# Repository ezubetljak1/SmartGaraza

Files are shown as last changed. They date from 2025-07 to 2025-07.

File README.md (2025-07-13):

# IoT Pametni Garažni Sistem

U današnje doba Interneta Stvari, svakodnevni uređaji postaju pametniji i povezaniji. Ovaj projekt pretvara običnu garažu u siguran i jednostavan sistem za pristup integracijom:

- **Višefaktorski pristup**: RFID čip, PIN kod ili mobilna aplikacija  
- **Evidencija pristupa**: Svaki ulaz/izlaz bilježi se sa vremenom pristupa i ID‑om korisnika  
- **Zaštita od neovlaštenih upada**: Automatsko zaključavanje i obavijest vlasniku o pokušaju pristupa  
- **Daljinsko upravljanje**: Otvarajte ili nadgledajte garažu putem aplikacije, odakle god želite

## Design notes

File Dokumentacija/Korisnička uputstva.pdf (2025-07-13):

Univerzitet u Sarajevu
Elektrotehnički fakultet

Ugradbeni sistemi (RI/TK) 2024/25

# Sistem za upravljanje pristupom garaži pomoću IoT tehnologija

## Korisnička uputstva

Članovi tima:

Dalila Tanković | 19665
Emina Hadžić | 19798
Emina Zubetljak | 19676
30. 6. 2025. god.

## Sadržaj

## 1 O proizvodu

Ovim putem Vam se zahvaljujemo što ste se odlučili za korištenje našeg pametnog sistema za kontrolu garažnih vrata. Naš cilj je da uživate u svim pogodnostima koje Vam on donosi, najprije u sigurnosti, pouzdanosti, te jednostavnosti korištenja.

Ovaj sistem koristi najnovije tehnologije iz oblasti ugradbenih mikrokontrolera i Interneta Stvari, kako bi Vam omogućio:

- jednostavno i brzo otvaranje garažnih vrata,
- sigurnu kontrolu pristupa za članove domaćinstva,
- daljinsko upravljanje putem mobilne aplikacije,
- zaštitu od neovlaštenog ulaska zahvaljujući ugrađenom alarmnom sistemu.

Uputstva koja slijede Vam služe za pravilno korištenje i održavanje uređaja.

## 2 Sastav sistema

Sistem se sastoji od više komponenti. Detaljnije možete pročitati u idućoj tabeli.

Tabela 1: Komponente i namjene u sistemu garaže

Komponenta | Namjena
picoETF kontroler | Vanjska jedinica – kontrola pristupa
Ultrazvučni senzor | Detekcija vozila ispred garaže
RFID čitač | Očitavanje beskontaktnih kartica
Tastatura | Unos sigurnosnog PIN koda
Piezo zvučnik | Alarmni sistem
LED dioda | Vizuelni indikator statusa alarma
Servo motor | Otvaranje i zatvaranje vrata
Touch senzor | Lokalno otvaranje/zatvaranje vrata
picoETF kontroler | Unutrašnja jedinica garaže

## 3 Sigurnosna upozorenja

Upozorenje! Nikada nemojte gurati ili silom pomjerati vrata dok ih upravlja motor.

Napomena! Samo osobe sa validnom karticom ili PIN kodom mogu otvoriti vrata.

Preporuka! Koristite mobilnu aplikaciju za nadzor i u hitnim slučajevima.

## 4 Osnovne upute

### 4.1 Dolazak vozila

Kada automobil priđe garaži, ultrazvučni senzor automatski detektuje prisustvo vozila na udaljenosti manjoj od 7 cm i pokreće postupak validacije.

### 4.2 Identifikacija korisnika

U ovom koraku imate 3 opcije.

a) RFID identifikacija

Korisnik prinosi svoju RFID karticu čitaču. Sistem očitava jedinstveni kod kartice.

Ako je kartica validna - vrata se automatski otvaraju.

Ako je kartica nepoznata - aktivira se alarm i ulaz se onemogućava.

b) PIN autentifikacija

Korisnik unosi četverocifreni PIN kod koristeći tastaturu pored garaže. Potvrda se vrši pritiskom na taster „#”. U slučaju da ste pogrešno unijeli PIN i ne želite ga potvrditi, možete restartovati unos pritiskom na taster „*”.

Sistem dozvoljava maksimalno 3 uzastopna neuspjela pokušaja. Nakon trećeg pogrešnog unosa:

- Aktivira se alarm.
- Dalja upotreba tastature se privremeno blokira.
- Korisnik mora ugasiti alarm putem aplikacije da bi resetovao stanje.
c) Mobilna aplikacija

Putem mobilne aplikacije korisnik može:

- Slati naredbe za otvaranje i zatvaranje vrata,
- Gasiti alarm,
- Primati obavijesti o statusu sistema,
- Pratiti historiju ulaska vozila u garažu.

### 4.3 Otvaranje i zatvaranje vrata

Otvaranje i zatvaranje vrata je automatizovano korištenjem servo motora.

### 4.3.1 Otvaranje

Dešava se automatski nakon uspješne autentifikacije. Alternativno, vrata možete otvoriti putem mobilne aplikacije. Nemojte pritiskati dugme za otvaranje vrata ako niste sigurni da želite da se isto ostvari.

### 4.3.2 Zatvaranje

U unutrašnjosti garaže se nalazi touch senzor kojim možete zatvoriti vrata. Alternativno, možete zatvoriti vrata putem aplikacije. U slučaju da niste zatvorili vrata 2 minute nakon otvaranja istih, vrata se automatski zatvaraju.

### 4.4 Alarmni i sigurnosni sistem

Ugrađen je Piezo generator zvuka, kao i LED indikator.

Alarm se aktivira u idućim scenarijima:

- Prislonjena je nepoznata RFID kartica
- Desila su se tri uzastopna pogrešna unosa PIN koda

Alarm ostaje aktivan:

- sve dok korisnik ne pošalje naredbu za isključenje putem mobilne aplikacije

## 5 Komunikacija i mobilna aplikacija

Sistem koristi MQTT protokol i sljedeće komunikacijske kanale.

Tabela 2: MQTT teme i poruke za garažu

Topic | Opis funkcionalnosti | Vrijednosti poruka
garaza/vrata | Upravljanje garažnim vratima. Na osnovu poruke se vrata otvaraju ili zatvaraju. | open, close
garaza/alarm/aktivan | Obavještava sistem (ili korisnika) da je alarm aktiviran (npr. neuspješan RFID ili PIN). | aktivan
garaza/alarm/ugasiti | Signal za deaktivaciju alarma ako korisnik uspješno otkuca PIN ili preko aplikacije. | alarm_off
garaza/validacija/start | Inicira provjeru identiteta korisnika. Aktivira tastaturu i displej nakon što senzor detektuje vozilo. | start
garaza/vrata/user | Prosljeđuje identifikaciju korisnika (npr. RFID broj ili PIN) u sistem radi evidencije ili logike. | Broj RFID kartice ili PIN

Aplikacija mora imati pristup internetu kako bi komunicirala sa sistemom. Sistem mora imati pristup internetu.

## 6 Rješavanje mogućih problema

U idućoj tabeli Vam navodimo potencijalne probleme koji bi mogli nastati pri korištenju sistema, kao i načine rješavanja istih.

Tabela 3: Pregled problema, mogućih uzroka i rješenja

Problem | Mogući uzrok | Rješenje
Vrata se ne otvaraju | Vozilo nije dovoljno blizu senzoru | Priđite bliže garaži
RFID kartica izaziva alarm | Nije registrovana u sistemu | Obratite se administratoru
PIN ne radi | Pogođena blokada tastature nakon grešaka | Reset iz aplikacije
Alarm ne prestaje | Nije poslana komanda alarm_off | Uđite u aplikaciju i deaktivirajte alarm
Aplikacija ne reaguje | Nema internetske konekcije | Provjerite Wi-Fi signal
Alarm se aktivirao, ali nije stigla notifikacija na mobitel | Niste bili povezani na internet | Povežite se na internet i resetujte aplikaciju

## 7 Održavanje

- Povremeno očistiti RFID čitač i tastaturu.
- Održavati pristup Wi-Fi mreži.
- Povremeno pregledati servo motor na fizička oštećenja.

## 8 Podrška i kontakt

Za sve tehničke upite, proširenja sistema ili prijavu greške, kontaktirajte razvojni tim putem fakulteta ili zaduženog asistenta.

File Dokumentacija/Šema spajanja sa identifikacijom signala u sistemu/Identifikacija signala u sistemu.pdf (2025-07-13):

Univerzitet u Sarajevu
Elektrotehnički fakultet

Ugradbeni sistemi (RI/TK) 2024/25

# Sistem za upravljanje pristupom garaži pomoću IoT tehnologija

## Identifikacija signala u sistemu

### Članovi tima:

Dalila Tanković | 19665
Emina Hadžić | 19798
Emina Zubetljak | 19676
30. 6. 2025. god.

Tabela 1: Pregled signala i njihovih funkcija u sistemu garaže

Naziv signala | Tip | Fizički tip | Opis funkcije
RFID čitač | Ulaz | Serijski (SPI) | Skenira RFID tag i identifikuje korisnika.
Matrična tastatura | Ulaz | Digitalni | Omogućava unos PIN koda za autentifikaciju.
Ultrazvučni senzor | Ulaz | Digitalni (Trig/Echo) | Mjeri distancu i detektuje prisustvo vozila ispred garaže.
Touch senzor (taster) | Ulaz | Digitalni | Detektuje pritisak tastera iz unutrašnjosti garaže za otvaranje/zatvaranje vrata.
MQTT poruke (open/close/start) | Ulaz | Softverski signal (IoT, MQTT) | Komande za pokretanje sistema, otvaranje ili zatvaranje vrata.
Piezo zvučnik | Izlaz | Digitalni | Aktivira se u slučaju alarma.
LED dioda | Izlaz | Digitalni | Vizuelni indikator aktiviranog alarma.
Servo motor | Izlaz | PWM | Mehanički otvara i zatvara vrata garaže.
7-segmentni displej | Izlaz | Digitalni | Prikazuje uneseni PIN.

MQTT poruke
(open, user,
alarm)
Izlaz | Softverski signal (IoT, MQTT)

Obavještenja i naredbe poslane drugom mikrokontroleru ili aplikaciji.

1

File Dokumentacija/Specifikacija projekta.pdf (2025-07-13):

Univerzitet u Sarajevu
Elektrotehnički fakultet

Ugradbeni sistemi (RI/TK) 2024/25

# Sistem za upravljanje pristupom garaži pomoću IoT tehnologija

## Specifikacija projekta

### Članovi tima:

Dalila Tanković | 19665
Emina Hadžić | 19798
Emina Zubetljak | 19676
7. 6. 2025. god.

## Sadržaj

## 1 Uvod i motivacija

### 1.1 Kratki opis problema i potrebe

U današnjem dobu Interneta Stvari, povezanost uređaja i sistema postaje sve značajnija za svakodnevni život i poslovne procese. Pametni sistemi u kućama postaju sve češći i pristupačniji, a broj prednosti koje donose korisnicima je gotovo neograničen.

Garažni sistemi u svojoj osnovi svakodnevno ispunjavaju svrhu zaštite vozila i njihovih skladištenja. Ipak, s razvojem Interneta Stvari, otvara se mogućnost dodatnih funkcionalnosti koje mogu značajno poboljšati korisničko iskustvo, prije svega kroz unapređenje sigurnosnih mehanizama.

Integracijom IoT komponenti, pametna garaža nudi jednostavniju i pregledniju kontrolu pristupa. Dovoljno je aktivirati mobilni uređaj, dodirnuti RFID čip, ili ukucati odgovarajući PIN, da bi se vrata otvorila. Osim lakšeg korištenja, ona nudi i dodatnu evidenciju pristupa. Svaki ulaz i izlaz se bilježi s vremenom i identifikacijom korisnika, što vlasniku daje uvid u korištenje prostora i potencijalne neočekivane situacije. Pokušaj neovlaštenog pristupa rezultira trajnijim zaključavanjem garaže i slanjem obavijesti vlasniku, uz podršku alarmnog sistema.

### 1.2 Ciljevi projekta

Cilj ovog projekta je realizacija pametnog sistema za kontrolu pristupa garaži korištenjem dvije različite mikrokontrolerske platforme, senzora pokreta, RFID čitača i matrične tastature. Sistem omogućava automatsko prepoznavanje prisustva vozila ispred garaže, višefaktorsku autentifikaciju korisnika, evidenciju pristupa, alarmne notifikacije pri pokušaju neovlaštenog pristupa, te jednostavan mehanizam za izlaz iz garaže. Korištenje mobilne aplikacije omogućava da se detaljno prati stanje sistema i historija korištenja.

## 2 Opis sistema

### 2.1 Osnovno ponašanje

Počevši od ulaza u garažu, sistem koristi senzor pokreta da prepozna nadolazeće vozilo. Nakon prepoznavanja istog, omogućava se procedura otključavanja garažnih vrata. Otključavanje istih je moguće uraditi kroz mobilnu aplikaciju, koristeći RFID skener i odgovarajući prepoznati čip, ili ukucavanjem PIN-a na matričnoj tastaturi.

Nakon dopuštenog ulaza, vanjski mikrokontroler komunicira sa unutrašnjim, čija je svrha da se pobrine za samo otvaranje vrata. Vrata se otvaraju koristeći servo motor. Nakon što se vrata otvore i automobil uđe u parking garažu, vrata se zatvaraju pritiskom na taster u unutrašnjosti garaže, ili koristeći mobilnu aplikaciju.

Da bi se omogućio ponovni izlazak iz garaže, koristi se mobilna aplikacija ili taster u njenoj unutrašnjosti da se vrata otvore. Ona se automatski zatvaraju kroz određeni vremenski period, ili koristeći mobilnu aplikaciju.

Alarmni sistem se aktivira u slučaju skeniranja nevalidnog RFID čipa, ili ukucavanja pogrešnog PIN-a na matričnu tastaturu tri puta zaredom. Pored aktiviranja alarma, pređe se u mod zaključavanja, kojim se ne dopušta ulaz u garažu na bilo koji način. Korisniku se putem mobilne aplikacije javlja da je došlo do pokušaja neovlaštenog pristupa, nakon čega može da obustavi alarm i izađe iz moda zaključavanja putem mobilne aplikacije.

### 2.2 Neophodne komponente

Na osnovu prethodnog opisa ponašanja, moguće je zaključiti da su neophodne iduće komponente:

Komponenta | Svrha
picoETF razvojni sistem | Glavna upravljačka jedinica izvan garaže
Ultrazvučni senzor | Detekcija prisutnosti vozila ispred garaže
RFID čitač | Identifikacija korisnika putem RFID kartica ili oznaka
Matrična tastatura | Ukucavanje PIN-a za ulaz u garažu
Piezo pretvarač zvuka | Alarmni sistem
LED dioda | Indikator pokrenutog alarmnog sistema
Raspberry Pi 2B | Upravljačka jedinica za unutrašnjost garaže
Servo motor | Mehaničko otvaranje i zatvaranje garažnih vrata
Taster | Zatvaranje i otvaranje garaže iz njene unutrašnjosti

Tabela 1: Osnovne komponente sistema i njihove svrhe

## 3 Opseg i funkcionalni zahtjevi

### 3.1 Autentifikacija vozila

Kao što je već ukratko spomenuto, cilj je da postoji više načina da se odobri ulaz korisnika u garažu. Kada senzori detektuju prisustvo vozila, sistem omogućava korisniku da pristupi unosu putem RFID skenera ili ručnog unosa PIN koda. Samo validni čipovi ili ispravni PIN kodovi omogućavaju otvaranje garažnih vrata. U slučaju da se koristi nevalidan RFID čip ili se tri puta zaredom unese pogrešan PIN na matričnoj tastaturi, aktivira se sigurnosni alarm. Također je moguće omogućiti ulaz u garažu direktno posredstvom mobilne aplikacije. Ovo postaje naročito korisno ukoliko garaži želi da pristupi osoba kojoj trebamo dopustiti ulaz, ali kojoj ne želimo izravno reći naš sigurnosni PIN.

### 3.2 Kontrola otvaranja i zatvaranja vrata

Otvaranje garažnih vrata upravlja se servo motorom koji se aktivira nakon uspješne autentifikacije korisnika. Vrata ostaju otvorena sve dok korisnik ne pritisne poseban taster za zatvaranje, čime se servo motor pokreće i vrata se zatvaraju. Za izlazak iz garaže, korisnik jednostavno pritisne isti taster, bez potrebe za dodatnom autentifikacijom, pod uvjetom da je vozilo već unutar garaže i da je pristup ranije odobren. Nakon što se vrata otvore za izlazak, sistem automatski pokreće tajmer koji, nakon određenog vremenskog intervala, zatvara vrata kako bi se osigurala dodatna sigurnost. Ovakav način upravljanja omogućava potpunu kontrolu korisniku nad trajanjem otvorenosti vrata, uz dodatnu sigurnost zahvaljujući automatskom zatvaranju. Svaki događaj otvaranja i zatvaranja vrata se evidentira u aplikaciji, što omogućava pregled historije pristupa i bolju kontrolu nad sigurnošću garaže.

### 3.3 Komunikacija i IoT integracija

U okviru sistema komuniciraju dvije glavne upravljačke jedinice, tj. dva različita mikrokontrolera koja služe za kontrolu vanjskog i unutrašnjeg dijela sistema respektivno. Pored toga, oba sistema komuniciraju sa mobilnom aplikacijom, na osnovu koje se može vidjeti i upravljati stanjem sistema u bilo kojem momentu. Također se pamti historija korištenja, odnosno bilježe se svi ulazi i izlazi iz garaže, što značajno doprinosi sistemu koji ima više korisnika. Sistemi će međusobno, odnosno sa mobilnom aplikacijom, komunicirati posredstvom MQTT protokola.

### 3.4 Alarmna i sigurnosna funkcionalnost

Sistem je opremljen sigurnosnim mehanizmima koji štite garažu od neovlaštenog pristupa. Ukoliko se tri puta zaredom unese pogrešan PIN na matričnoj tastaturi ili se koristi nevalidan RFID čip, automatski se aktivira alarmni sistem. Alarm se oglašava blinkanjem crvene LED diode koja vizuelno upozorava na pokušaj neovlaštenog ulaska. Istovremeno, u aplikaciju se šalje notifikacija korisniku ili administratoru sistema kako bi se omogućila pravovremena reakcija. Ovaj sigurnosni mehanizam doprinosi zaštiti garaže i evidenciji svih pokušaja neautorizovanog pristupa.

## 4 Moguća proširenja funkcionalnih zahtjeva

U nastavku navodimo dodatne funkcionalnosti koje bi bile izvodljive u okviru našeg projekta, s ciljem poboljšanja postojećeg modela.

### 4.1 Automatsko zatvaranje vrata nakon određenog vremena

Umjesto da je jedini način zatvaranja vrata posredstvom korisničkog djelovanja (taster ili mobilna aplikacija), moguće je dodati opciju da se vrata automatski zatvaraju nakon određenog vremena i bez djelovanja korisnika. Ovo povećava sigurnost i olakšava korištenje sistema sa strane korisnika, u slučaju da vrata greškom ostaju otvorena nakon ulaza u garažu. Ovo bi skinulo dio odgovornosti sa korisnika sistema, te bi se smanjio broj neželjenih situacija u kojima korisnik eventualno zaboravi koristiti taster nakon ulaska u garažu.

### 4.2 Višekorisnički sistem sa različitim nivoima pristupa

Implementacija različitih korisničkih profila sa posebnim pravima bi također dodatno doprinijela sistemu koji ima veći broj korisnika. Moguće je svakom dodijeliti posebni PIN, tako da se u svakom momentu zna tačno koji korisnik je pristupio prostoru, čak iako odluči da ne skenira svoj RFID čip. Moguće je na osnovu korisničkih profila dodijeliti različita dozvoljena vremena pristupa prostoru ili različit broj pokušaja autentifikacije.

### 4.3 Integracija senzora za detekciju prepreka

Dodavanjem dodatnog ultrazvučnog ili infracrvenog sistema u unutrašnjosti garaže bi se omogućila implementacija sistema za detekciju prepreka, koji onemogućava zatvaranje vrata ukoliko mu se vozilo ili neki drugi objekat nalazi na putu. Ovim se doprinosi na sigurnosti pri korištenju sistema koji inače zatvara vrata posredstvom tajmera sa određenim vremenskim intervalom, i sprječava neželjene situacije u kojima se neki objekat ošteti jer se našao u prolazu kada je prošao vremenski interval za izlaz iz garaže.

### 4.4 Sistem za automatsko osvjetljenje unutrašnjosti garaže

Ugradnjom senzora svjetlosti ili pokreta u unutrašnjosti garaže, moguće je implementirati automatsko osvjetljenje kada se vozilo ili osoba nalazi u garaži. Time se znatno poboljšava korisničko iskustvo.

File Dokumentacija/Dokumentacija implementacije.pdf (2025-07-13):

Univerzitet u Sarajevu
Elektrotehnički fakultet

Ugradbeni sistemi (RI/TK) 2024/25

# Sistem za upravljanje pristupom garaži pomoću IoT tehnologija

## Dokumentacija implementacije

Članovi tima:

Dalila Tanković | 19665
Emina Hadžić | 19798
Emina Zubetljak | 19676
30. 6. 2025. god.

## Sadržaj

## 1 Uvod

Kao što je prethodno navedeno u specifikaciji, cilj ovog projekta je bio da se implementira sistem pametne garaže, koja rješava mnoge korisničke probleme koji se pojavljuju sa korištenjem standardnog sistema. Opremljena sa cjelokupnim sigurnosnim sistemom, garaža omogućava višestruk način za validaciju identiteta vozača. U slučaju pokušaja nedozvoljenog pristupa, aktivira se alarmni sistem koji zaključava garažu, odnosno onemogućen je bilo koji način pristupa istoj. Sistem se uvezuje korištenjem Android mobilne aplikacije, kroz koju je moguće gasiti aktivirani alarm. Također je moguće otvarati i zatvarati vrata bez obzira gdje se korisnik nalazi, i analizirati historiju ulaza u garažu, što postaje naročito korisno u slučaju više korisnika.

Pri tehničkoj implementaciji projekta je posebna pažnja stavljena na efektivnu implementaciju svih dijelova projekta, budući da je zbog postavke problema u mnogim scenarijima neophodno da sistem istovremeno radi više operacija, odnosno da je spreman da odgovori na različite zahtjeve. Također, sam sistem se sastoji od dva mikrokontrolera, odnosno picoETF razvojna sistema, koji kontrolišu vanjski i unutrašnji dio garaže respektivno. Stoga je bilo neophodno omogućiti efektivnu komunikaciju između njih, da bi sistem djelovao kao cjelina. Komunikacija cjelokupnog sistema je bazirana na MQTT protokolu.

U nastavku je detaljno objašnjena izvedba tehničkog dijela, razdvojena po segmentima sistema.

### 1.1 Korištene biblioteke

U okviru sistema se koriste biblioteka machine, za rad sa GPIO razvojnog sistema. U okviru nje su korištene klase PWM, Timer, te Pin.

Korištene su i biblioteke umqtt.simple, network i time, zbog realizacije MQTT protokola i kontrole toka programa sa pauzama.

Dodatne biblioteke uključuju urandom za nasumične brojeve i mfrc522 za rad sa RFID čitačem.

## 2 MQTT protokol

Kao što je već spomenuto, sistem se sastoji iz dva mikrokontrolera koja međusobno komuniciraju, a oba komuniciraju i sa mobilnom aplikacijom. Za način realizacije spomenute komunikacije odabran je MQTT protokol.

Na oba mikrokontrolera su definisane funkcije connect_wifi, koje služe da se mikrokontroler spoji na definisanu WiFi mrežu. Za ovu svrhu se koristi klasa WLAN iz biblioteke network, zajedno sa metodama active, isconnected i connect.

Navedena funkcija se poziva iz funkcije mqtt_setup, u okviru koje se i konfiguriše MQTT klijent. Postavlja mu se odgovarajući callback, u okviru kojeg se parsiraju poruke i njihove vrijednosti, zajedno sa temom na koju su poslane, te se vrše odgovarajuće akcije u sistemu nakon primanja istih. Dakle, poziva se metoda set_callback i connect. Spajanje se vrši u okviru try bloka, budući da se može desiti da MQTT spajanje ne uspije.

Nakon spajanja je neophodno pretplatiti se na sve teme sa kojih odgovarajući mikrokontroler prima korisne informacije. Za pretplatu na temu se koristi metoda subscribe.

Nakon odgovarajuće konfiguracije, mikrokontroler je spreman da reaguje na pristigle poruke kroz poziv metode check_msg u glavnoj petlji. U slučaju kada mikrokontroler treba objaviti poruku na neku temu, koristi se metoda publish. U dijelovima koji slijede će biti definisana sva komunikacija koja se zapravo odvija u okviru sistema.

## 3 Validacija pristupa

Sistem može validirati pristup kroz validnu RFID karticu, ili unos tačnog PIN-a na matričnoj tastaturi. U ovoj fazi sistem izvršava nekoliko operacija istovremeno. Naime, sistem mora biti spreman da registruje RFID karticu koja je prislonjena, a također mora reagovati na eventualne pritisnute tipke matrične tastature, koje onda prikazuje na 7-segmentnom displeju. Jasno je da prosto korištenjem pristupa polling-a, odnosno prozivanja svake komponente individualno, sistem ne bi bio u stanju da radi efektivno. To se dešava iz razloga što bi se sekvencijalno radila jedna, pa druga operacija. Ova činjenica je pogoršana time da je skeniranje RFID kartice zapravo blokirajući poziv, a ne asinhroni. Odnosno, svaki put kad se poziva procedura za čitanje sa RFID čitača, sistem mora čekati na rezultat. U slučaju lošeg tajminga bi se vrlo lako moglo dešavati da sistem reaguje presporo, odnosno da eventualno ne registruje pritiske nekih tipki ili skeniranja kartice jer se u tom trenutku „bavio” onom drugom operacijom, pogotovo kad se uzme u obzir da je potrebno softverski riješiti problem debouncing-a tipki na matričnoj tastaturi, koje bi uvodile dodatne pauze u okviru izvršavanja glavne petlje. Uz to sve se mora i uzeti u obzir da prikaz cifara na displeju mora biti konzistentan, i dešavati se iznimno brzo, da ne bi došlo do treptanja koje je vidljivo ljudskom oku.

Iz svih navedenih razloga je odlučeno da se problematika riješi primarno korištenjem sistema prekida.

### 3.1 Unos PIN-a

### 3.1.1 Matrična tastatura

Jasno je da je za unos na matričnoj tastaturi potrebno velikom brzinom skenirati matričnu tastaturu, da bi se prepoznala pritisnuta tipka. Budući da ne želimo da blokiramo glavnu petlju programa, ova procedura se vrši posredstvom periodičnog tajmera.

Vođeni iskustvom stečenim u okviru rada na laboratorijskim vježbama, primijećeno je da pri korištenju standardne procedure za čitanje matrične tastature u kombinaciji sa timerima za displej i unos često izaziva problem ghosting-a. Ghosting na matričnoj tastaturi nastaje zbog nepoželjnih povratnih strujnih puteva u nediodiranoj matričnoj tastaturi. U praksi, dešava se da struja „iscuri” kroz susjedne linije i izazove lažni signal na nekom drugom presjeku, te se registruje pritisak više tipki, iako je u realnosti aktiviran samo jedan taster. Stoga je u okviru ovog projekta implementirana nešto kompleksnija, ali znatno pouzdanija „ghost-free” implementacija.

Implementacija izvedena u projektu kombinuje nekoliko ideja koje doprinose pouzdanijem skeniranju matrične tastature, a one uključuju:

- „two-way cross check”; ova ideja podrazumijeva dvostruko provjeravanje pritisnute tipke, pri čemu se u prvom prolazu pinovi redova koriste kao izlazni i kolone kao ulazni. U drugom prolazu se izvrši rekonfiguracija pinova, te se sada redovi koriste kao ulazni pinovi, a kolone kao izlazni.
- „N-sample streak debounce”; podrazumijeva da se tastatura skenira više puta uzastopno velikom brzinom, te da se pritisnuta tipka prizna samo ukoliko je u N prolaza registrovana ista tipka svaki put.

Prvi dio je implementiran u okviru pomoćne funkcije single_scan, koja služi za jedan „two-way” prolaz matrične tastature. Ona kao povratnu vrijednost vraća uređenu trojku, koja predstavlja indeks reda, indeks kolone, te tipku koja se nalazi u tom redu i koloni matrične tastature. Kao što je već rečeno, prvi prolaz služi za odabir kandidata za pritisnutu tipku. Jedan prolaz podrazumijeva standardno skeniranje matrične tastature, u kojem se postepeno svaki red, koji je trenutno izlazni pin, postavlja na high, provjerava se da li je aktivna neka od kolona, koja je deklarisana kao ulazni pin, te ukoliko je pronađen kandidat za tipku, izlazi se iz petlje. Ukoliko nije pronađen nikakav kandidat, ili ukoliko je više kolona detektovano kao aktivno, odmah se izlazi iz funkcije uz vraćanje uređene trojke gdje su svi elementi None, budući da je u tom scenariju ili detektovan ghosting, ili nijedna tipka nije aktivirana.

Nakon prvog prolaza se vrši rekonfiguracija pinova na idući način:

# rekonfiguracija pinova

for rp in row_pins: rp.init(Pin.IN, Pin.PULL_DOWN)
for cp in col_pins: cp.init(Pin.OUT)

Sada se vrši drugi prolaz, pri čemu se u obzir uzima samo kolona koja sadrži kandidata iz prethodnog prolaza. Provjerava se da li je u drugom prolazu detektovan isti kandidat, te se pinovi se vraćaju na izvornu konfiguraciju. Što se tiče detekcije istog kandidata, ukoliko jeste, vraća se trojka sa tim redom, kolonom i znakom, a ukoliko nije, ponovo se vraća trojka None.

Rezultat prethodne funkcije koristi funkcija scan_keypad, koja predstavlja glavni ISR za matričnu tastaturu, i ona se i prosljeđuje timeru. U okviru ove funkcije se vrši jedan „two-way scan” pozivom pomoćne funkcije, te se globalna varijabla _streak_count postavlja na jedan ukoliko je ova tipka detektovana po prvi put, odnosno vrijednost _streak_count se uvećava za jedan ukoliko je ta tipka već detektovana u prethodnom prolazu. Ovo se vrši posredstvom poređenja sa varijablom _last_rc. Zatim, ukoliko je vrijednost _streak_count dostigla vrijednost zahtijevanu kroz konstantu DEBOUNCE_STREAK (u ovom slučaju 4), zaista se prihvaća ta tipka, uz provjeru da li je u pitanju uzlazna ivica, zbog debouncinga.

Dakle da se sumira, za prihvaćanje tipke se matrična tastatura zapravo skenira četiri puta, gdje jedno skeniranje podrazumijeva duplu provjeru uz rekonfiguraciju pinova. Mada se ovo na prvu možda čini suvišno, ovakva implementacija se pokazala kao najbolja što se tiče pouzdanosti. Budući da se period tajmera postavlja na poprilično malu vrijednost od samo 20 ms, procedura se izvršava dovoljnom brzinom da se za korisnika tipka registruje instantno.

Nakon što se tipka registruje, iz ISR se poziva funkcija handle_key kojoj se proslijedi registrovana tipka. U okviru ove funkcije se vrši sama logika prepoznavanja PIN-a. Dakle, trenutna tipka se dodaje na uneseni pin, te ako je dužina unesenog pina jednaka predviđenoj od 4 znaka, i ako se pritisne tipka „#”, vrši se poređenje sa ispravnim PIN-om.

U slučaju ispravno unesenog PIN-a se isto vizuelno indicira na displeju tako što se 2 sekunde prikazuje blinkanje decimalnih tački. Nakon toga se pušta kratki zvuk sa generatora, i komunicira se sa unutrašnjim mikrokontrolerom da se vrata trebaju otvoriti. Ovo se vrši tako što se na odgovarajuću temu pošalje poruka. Također se šalje vrijednost koja naznačava koji korisnik je pristupio ulazu, da bi se ista informacija mogla zabilježiti na mobilnoj aplikaciji.

U slučaju pogrešno unesenog pina se dešava blinkanje znaka „-” na displeju i pamti se koja je to greška unosa po redu. Ako se desi treća uzastopna greška unosa, pali se alarmni sistem pozivom funkcije start_alarm, o čemu će detaljnije biti riječi u nastavku.

3.1.2 7-segmentni displej

Svaka pritisnuta tipka se treba adekvatno i prikazivati na displeju, što se također vrši posredstvom odvojenog tajmera koji je zadužen za ovu funkcionalnost.

Njegov callback je definisan kroz funkciju display_callback. Ova funkcija je prosto zadužena za prikaz cifre koja je trenutno na redu, što se pamti kroz globalnu varijablu current_digit. Drugim riječima, vrši se multipleksiranje za prikaz cifara. Na početku funkcije se gase sve cifre i segmenti. Zatim se ulazni pin parsira tako što se dopuni prazninama ukoliko je dužina trenutno manja od četiri. Trenutna cifra se ažurira tako što se postave odgovarajuće vrijednosti za segmente, koje su definisane u mapi DISPLEJ_MAPA. Ona kao ključ prima cifru, a kao rezultat vraća 7 bita koje predstavljaju odgovarajuće vrijednosti za svaki segment. Nakon postavljanja segmenata se pali cifra po redu i prelazi se na iduću cifru ažuriranjem globalne varijable.

Period ovog tajmera je postavljen na 5 ms, da bi se na ovaj način prikaz ažurirao dovoljno brzo da se ne uočava nikakvo treptanje prikaza ljudskim okom.

Što se tiče specijalnih slučajeva za vizuelni prikaz ispravnog i pogrešnog pina, definisane su funkcije flash_decimal_points i blink_minus. U okviru ovih funkcija se najprije deinicijalizira tajmer za displej. Zatim se 2s vrši prikazivanje odgovarajućih znakova u while petlji analognim pristupom kao ranije. Na kraju funkcija se ponovo inicijalizira tajmer. Na ovaj način je lakše implementirana logika prikazivanja na displeju, budući da je tajmer odgovoran samo za prikaz pina, a ne i za rezultat završenog unosa. To je urađeno iz razloga što se rezultat unosa treba vizuelno prikazivati 2s, što bi bilo teže uklopiti u logiku postojećeg tajmera.

### 3.2 RFID čitač

Biblioteka koja je korištena za realizaciju čitača je mfrc522, koja odgovara našem modulu. U okviru ove biblioteke se nalazi istoimena klasa, koja se koristi za inicijalizaciju čitača. Njoj se u konstruktoru proslijedi ID za korištene SPI pinove, tj. 0 u ovom slučaju, kao i odgovarajući pinovi.

Na početku funkcije rfid_callback se poziva metoda init koja resetuje MFRC522 i podešava osnovne registre (takt, modulaciju, timeout), te uključuje antenu za čitanje. Zatim se poziva metoda request sa odgovarajućim parametrom. Ona šalje ISO14443-A naredbu „REQIDL” da vidi da li se kartica nalazi u polju. Kao rezultat vraća stat (OK ili ERR) i tag_type (broj primljenih bita, tj. vrsta kartice). U slučaju da je detektovana kartica, što se prepoznaje po stat, poziva se metoda SelectTagSN. Ona kombinuje antikoliziju i selekciju, te kao rezultat vraća uid (4-bajtni jedinstveni ID kartice) i stat, koji ponovo govori je li UID uspješno pročitan.

Ako je UID ispravno pročitan, obrada se nastavlja dalje parsiranjem broja kartice. Lista bajtova uid se spakuje u 32-bitni cijeli broj zapisan u little-endian formatu. Zatim se vrši usporedba sa dozvoljenom karticom koja je registrovana u sistemu. Ovisno od toga da li je kartica validna ili ne, vrši se slična procedura kao i kod unosa pina.

Za validnu karticu se pušta kratki zvuk na generatoru, te se na odgovarajuće teme objavljuju poruke o otvaranju vrata, te o korisniku koji je pristupio ulazu. Ako kartica nije registrovana u sistemu, pali se alarm.

Sama procedura se poziva u glavnoj petlji programa svakih 1.5 s. Razlog zašto ova funkcionalnost nije prepuštena tajmeru je već spomenut - funkcije za čitanje u okviru korištene biblioteke su blokirajući pozivi. Stoga, ne bismo zapravo ništa „dobili” korištenjem tajmera. Taj tajmer bi zapravo remetio unos odnosno prikaz pina na displeju, zato jer se presporo izvršava. Budući da je ovo jedina operacija koja se izvršava u glavnoj petlji, pored provjeravanja da li je došla MQTT poruka na neku od tema, i da se ona posredstvom statusnih varijabli zaista izvršava samo kada je neophodno, sistem je i dalje u stanju obavljati sve poslove efikasno.

### 3.3 Alarm

Aktiviranje alarma se vrši na vrlo jednostavan način kroz funkciju start_alarm. Prosto se vrijednost pina postavi na 1, ažurira se statusna varijabla alarm_active, te se također deinicijaliziraju aktivni tajmeri za tastaturu i displej, da bi se onemogućio unos pina dok traje alarm. Statusna varijabla alarm_active služi da se onemogući čitanje RFID kartice u glavnoj petlji.

Također se na odgovarajuću temu objavljuje poruka da je alarm trenutno aktivan. Ova poruka služi da bi se posredstvom mobilne aplikacije aktivirala notifikacija koja obavještava korisnika. Notifikacija stiže uz vibraciju mobitela, da bi se lakše uočila. Notifikacija dolazi na uređaj neovisno da li je mobilna aplikacija aktivna u tom momentu ili ne, budući da ona pozadinski sluša na upravo ovu MQTT poruku da bi pokrenula notifikaciju.

Gašenje alarma se vrši klikom na dugme u mobilnoj aplikaciji. Time se zapravo postavlja poruka na temu na koju je vanjski mikrokontroler pretplaćen. Dobijanjem ovakve poruke se aktivira callback za MQTT klijenta definisan u okviru funkcije on_mqtt. U slučaju da je primljena ispravna poruka, alarm se gasi funkcijom stop_alarm, u kojoj se također sistem vrati na prvobitno stanje sa aktivnim tajmerima i RFID čitanjem.

## 4 Senzor pokreta

Gledajući funkcionalnosti sistema, senzor pokreta nije neophodan da sistem radi. Razlog zašto je dodan senzor pokreta je zbog uštede energije. Naime, pri validaciji unosa sistem mora vršiti nekoliko operacija istovremeno, što kao rezultat može biti poprilično zahtjevno za CPU. Korištenjem senzora pokreta je moguće detektovati momenat kada se vozilo približi, te tek tada aktivirati proces validacije unosa.

Senzor pokreta je zapravo spojen na unutrašnji mikrokontroler, iz razloga što su svi pinovi vanjskog već bili zauzeti. Ultrazvučni senzor ima dva ključna pina, trigger i echo. Kada senzor primi kratki puls na trigger, on transmituje kratki ultrasonični puls, te se nakon toga sluša na eho. echo pin dobija vrijednost high koja traje do 25 ms ovisno od distance objekta, a ako se nikako ne detektuje objekat, pin ostane high do maksimalno 38 ms. Mjerenjem vremena za koje je vrijednost echo pina jednaka 1, u kombinaciji sa brzinom zvuka u zraku, moguće je izračunati udaljenost objekta.

Samo mjerenje distance se vrši u okviru funkcije mjeri. Funkcija započinje tako što se šalje kratki puls na pin trigger. Zatim se koristi funkcija time_pulse_us iz biblioteke machine da se računa ukupno vrijeme za koje je vrijednost echo pina jednaka 1. Distanca se računa kao proizvod tog vremena i brzine zvuka, podijeljeno sa 2, jer nam treba samo distanca u jednom smjeru. Kao rezultat se dobija distanca u cm. Ako distanca padne ispod 7 cm, to je znak da se automobil približio u pogled senzora. Tada se na MQTT temu šalje obavještenje, na osnovu kojeg vanjski mikrokontroler inicijalizira tajmere za unos i počinje sa validacijom.

## 5 Kontrola garažnih vrata

Fizičko otvaranje i zatvaranje vrata se vrši posredstvom servo motora kojeg kontroliše unutrašnji mikrokontroler. Sam servo motor je deklarisan kao PWM izlaz, da bi se mogla kontrolisati željena vrijednost ugla.

Najprije je definisana funkcija koja služi za mapiranje intervala. Servo motor ima opseg ugla od 0°do 180°. Željenu vrijednost ugla je potrebno mapirati na interval [0, 65535], budući da se duty cycle zadaje kao nepredznačni broj od 16b. U funkciji mapiranje_intervala se primjenjuje vrlo jednostavna formula, gdje su sve navedene vrijednosti parametri iste:

return (x - ulazni_min) *
(izlazni_max - izlazni_min)/(ulazni_max - ulazni_min) + izlazni_min

Za pravu kontrolu servo motora je definisana funkcija pisi_servo. Njoj se kao parametar šalje vrijednost željenog ugla, koji je u već navedenom opsegu. Standardni mikro servo motori, kao onaj koji je korišten u projektu, očekuju PWM signal sa fiksnom frekvencijom od 50 Hz, i sa podesivom širinom impulsa između oko 0.5 ms i 2.5 ms, koje odgovaraju vrijednostima 0°i 180°respektivno. U funkciji se najprije vrši mapiranje ugla na odgovarajuću širinu impulsa, te se vrijednost čuva u varijabli puls. Ovaj puls je u suštini vrijednost širine impulsa u milisekundama koju servo „razumije” kao svoj ciljni ugao. Zatim se ta širina impulsa pretvara u 16-bitni duty cycle, i ta vrijednost se zapravo postavlja kao duty na pinu servo motora.

Za otvaranje i zatvaranje vrata su definisane funkcije open_door i close_door. U okviru njih se prosto za zatvaranje vrata poziva funkcija pisi_servo sa parametrom 80, odnosno sa parametrom 180 za otvaranje vrata. Ove vrijednosti su se pokazale kao najadekvatnije za fizički servo koji je korišten za ovu realizaciju.

Otvaranje i zatvaranje vrata se primarno kontroliše primanjem MQTT poruka, o čemu je već bilo govora. U unutrašnjosti garaže se još nalazi touch senzor koji pruža alternativni način za postizanje iste svrhe. Na njegovom pinu je omogućeno izazivanje IRQ, a kao handler je napravljena funkcija touch_senzor. U njoj se prosto provjerava stanje vrata i izvrši odgovarajuća operacija; ako su vrata trenutno otvorena poziva se funkcija close_door, a ako su zatvorena poziva se open_door. Stanje vrata se prepoznaje kroz globalnu varijablu door_open čija se vrijednost ažurira u funkcijama adekvatno.

Zatvaranjem vrata se također inicijalizira tajmer koji je odgovoran za ultrazvučni senzor, budući da smo tada došli u stanje u kojem bi moglo biti neophodno ponovo čekati na približavanje vozila i unos vrijednosti.

Naposljetku, kao dodatni sigurnosni mehanizam je dodan tajmer nakon otvaranja vrata. Otvaranje vrata inicijalizira „one-shot” tajmer sa periodom 2 minute. U okviru njegovog callback-a se prosto provjerava da li su vrata i dalje otvorena, te ako jesu, zatvaraju se. Razlog za dodavanje ove mogućnosti je u slučaju da korisnik zaboravi fizički zatvoriti vrata nekom od akcija, vrata će se zatvoriti sama.

## 6 Mobilna aplikacija

Detalji implementacije mobilne aplikacije ovdje neće biti u potpunosti navedeni, budući da je ista obavljena u Kotlin programskom jeziku, i suštinski je nevezana za ovaj

predmet.

Aplikacija se sastoji od dva pogleda. Na glavnom pogledu su 4 dugmeta kojim se mogu obavljati operacije već spomenute u prethodnim dijelovima; otvaranje i zatvaranje vrata, gašenje aktivnog alarma, te pregled historije ulaza u garažu. Sve ove opcije koriste MQTT komunikaciju.

Na pogledu historije korištenja se prikazuje lista korisnika uz datum i vrijeme njihovog ulaza. U kodu je definisano ime korisnika koje je vezano za validnu RFID karticu u sistemu. U slučaju da korisnik pristupi garaži koristeći PIN, identitet mu je tada nepoznat, te se registruje samo da je ulaz izvršen posredstvom ukucavanja PIN-a.

Alarmni sistem funkcioniše tako što se korisnik obavijesti o istom bez obzira da li je aplikacija aktivna ili ne. Naime, na prvom pokretanju aplikacije se inicijalizira MQTT klijent i u pozadini se održava konekcija s istim. Stoga, aplikacija može reagovati na pristiglu poruku i kada nije upaljena direktno. Na ovaj način korisnik pouzdano dobija notifikacije kada se desi pokušaj neovlaštenog pristupa.

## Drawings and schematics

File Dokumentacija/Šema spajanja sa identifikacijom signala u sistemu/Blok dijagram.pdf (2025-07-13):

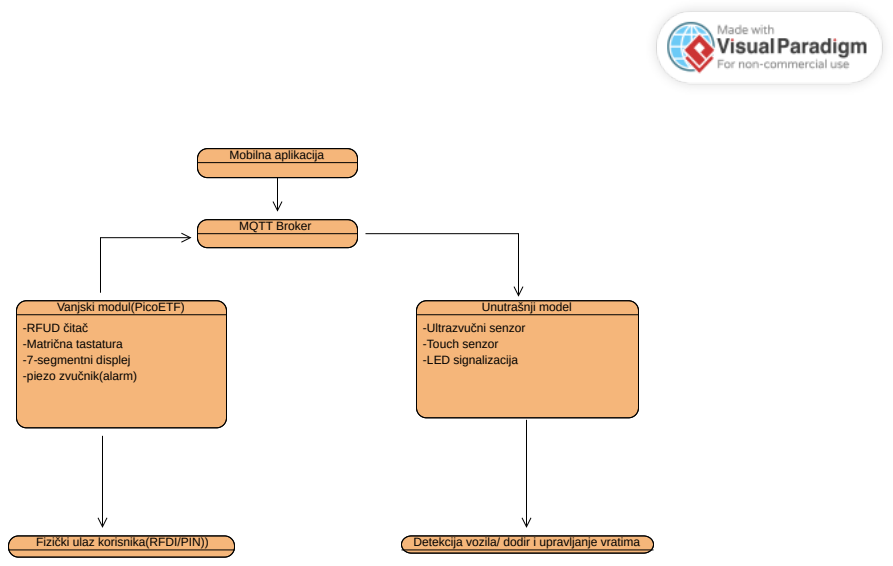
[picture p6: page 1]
Mobilna aplikacija; MQTT Broker; Unutrašnji model; -Ultrazvučni senzor -Touch senzor -LED signalizacija; Fizički ulaz korisnika(RFDI/PIN)); Detekcija vozila/ dodir i upravljanje vratima

Vanjski modul(PicoETF)
-RFUD čitač
-Matrična tastatura
-7-segmentni displej
-piezo zvučnik(alarm)

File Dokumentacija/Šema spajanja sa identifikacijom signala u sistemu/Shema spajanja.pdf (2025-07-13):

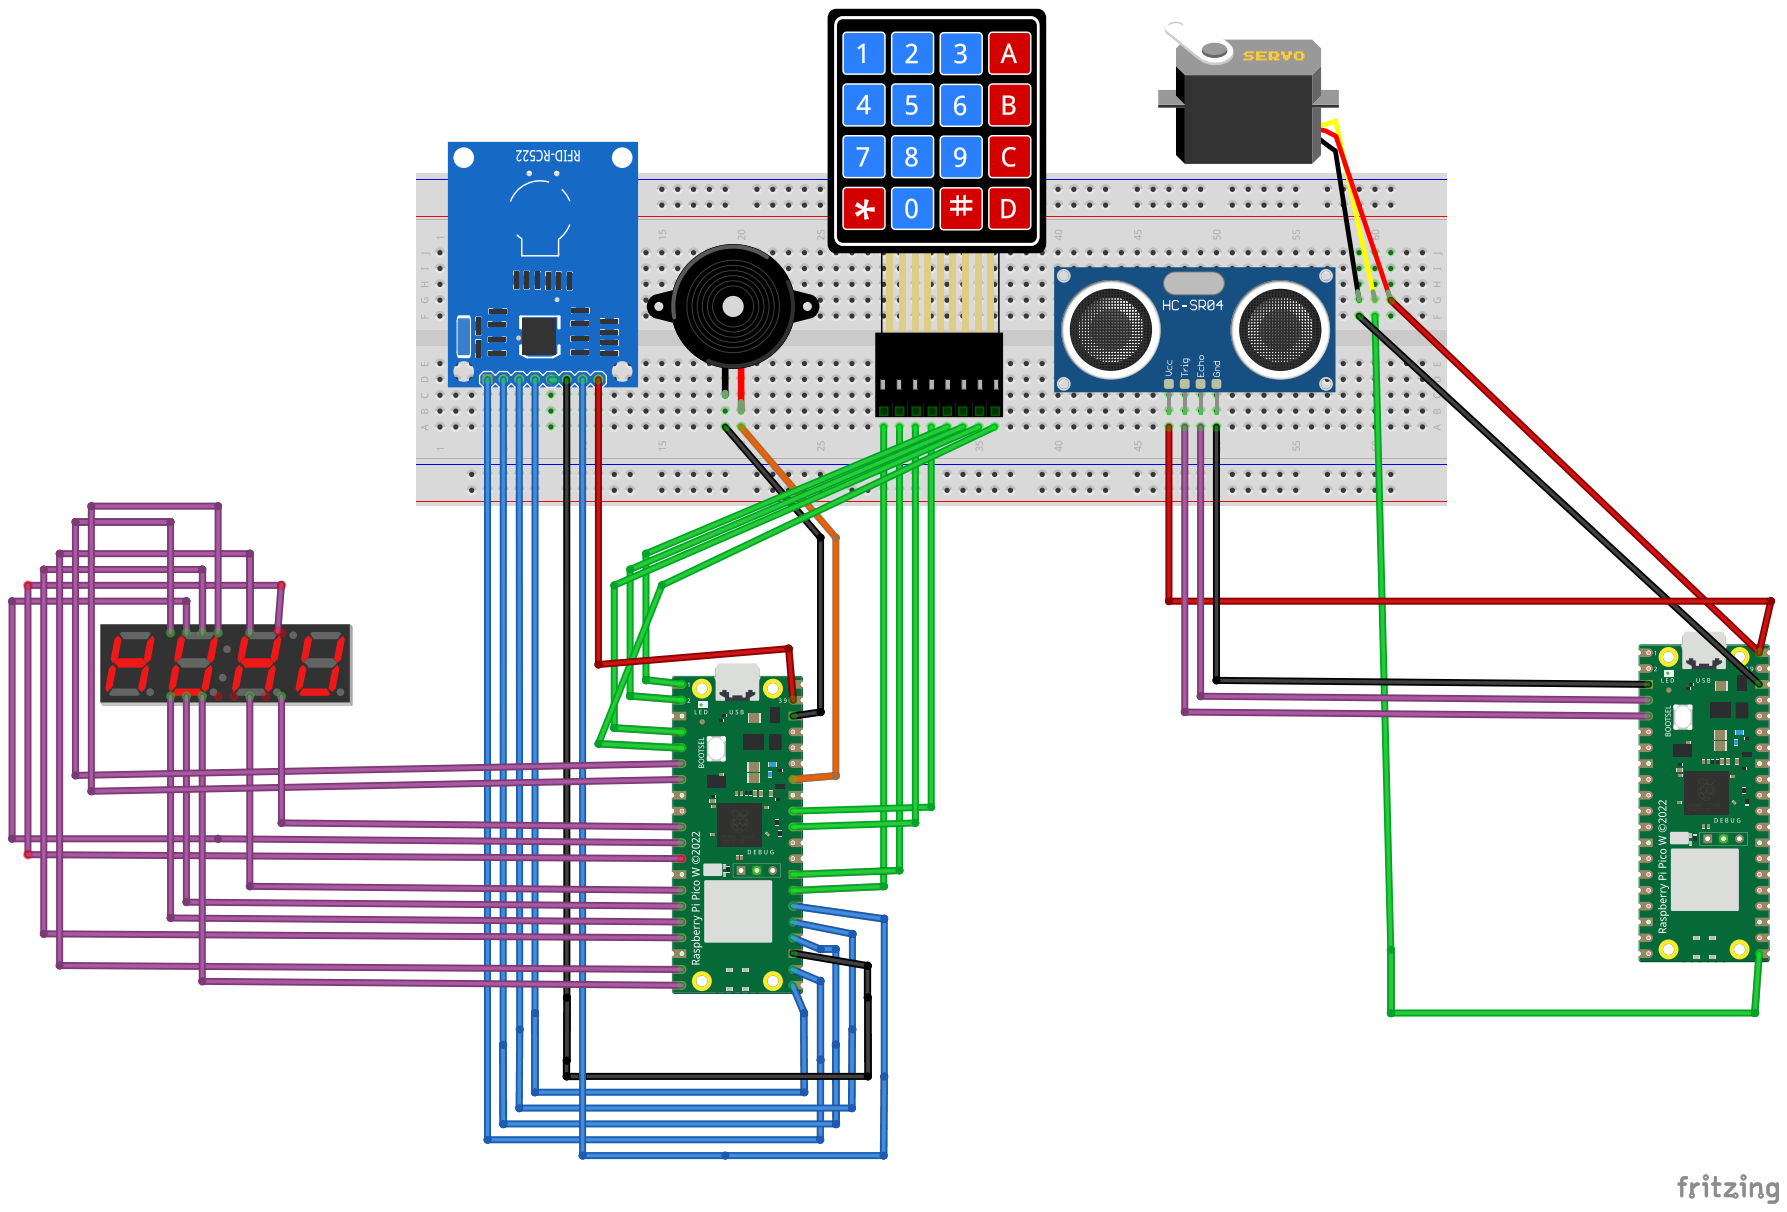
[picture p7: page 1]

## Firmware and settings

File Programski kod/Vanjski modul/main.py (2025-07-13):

from machine import Pin, Timer
import time, network
from umqtt_simple import MQTTClient
from mfrc522 import MFRC522
import urandom

# ----------------------------
# ---- VARIJABLE I PINOVI ----
# ----------------------------
# Generator zvuka
piezo = Pin(28, Pin.OUT)
piezo.low()

# Displej i tastatura
row_pins   = [Pin(p, Pin.OUT)             for p in (21,22,26,27)]
col_pins   = [Pin(p, Pin.IN, Pin.PULL_DOWN) for p in (0,1,2,3)]
digit_pins = [Pin(p, Pin.OUT)             for p in (4,5,6,7)]
seg_pins   = [Pin(p, Pin.OUT, Pin.PULL_UP) for p in (8,9,10,11,12,13,14)]
dp_pin     = Pin(15, Pin.OUT, Pin.PULL_UP)
dp_pin.value(1)

# RFID citac
reader = MFRC522(spi_id=0, sck = 18, cs =17, miso = 16, mosi=19, rst=20)

# ---- Varijable stanja ----
started = False # da li je zapocela validacija
input_pin = "" # ulazni pin koji se unosi 
_last_rc = (None, None) # prosla kombinacija red kolona
_streak = 0 # trenutni streak znakova
_debounced_rc = (None, None) 
current_digit = 0 # za multipleksiranje displeja
wrong_attempts = 0 # pogresni pokusaji unosa
alarm_active = False # je li alarm aktivan

# ---- Konstante ----
# Displej
DISPLEJ_MAPA = {
    0:(0,0,0,0,0,0,1), 1:(1,0,0,1,1,1,1), 2:(0,0,1,0,0,1,0),
    3:(0,0,0,0,1,1,0), 4:(1,0,0,1,1,0,0), 5:(0,1,0,0,1,0,0),
    6:(0,1,0,0,0,0,0), 7:(0,0,0,1,1,1,1), 8:(0,0,0,0,0,0,0),
    9:(0,0,0,0,1,0,0),
}

BLANK = (1,1,1,1,1,1,1)
MINUS = (1,1,1,1,1,1,0)

# Tastatura
matrix_keys = [
    ['1','2','3','A'],
    ['4','5','6','B'],
    ['7','8','9','C'],
    ['*','0','#','D']
]

DEBOUNCE_STREAK = 4

# RFID i PIN
DOZVOLJENA_KARTICA = "4159772003"
ISPRAVAN_PIN = '8273'

# ----------------
# ---- TIMERI ----
# ----------------
timer_keypad = Timer()
timer_display = Timer()
timer_mqtt = Timer()
# periodi u ms
SCAN_INTERVAL   = 20   
MUX_INTERVAL    = 5   
RFID_INTERVAL = 1500 

# ---------------------
# ---- WIFI I MQTT ----
# ---------------------
# WiFi podaci
SSID = 'ETF-WiFi-Guest'
PASSWORD = ''
# MQTT konekcija
BROKER = 'broker.hivemq.com'
random_suffix = "%04d" % (urandom.getrandbits(16) % 10000)
CLIENT_ID = b'picoETF_garaza' + random_suffix.encode()
client = MQTTClient(CLIENT_ID, BROKER)
# MQTT teme
T_ALARM_ACTIVE = b'garaza/alarm/aktivan'
T_ALARM = b'garaza/alarm/ugasiti'
T_VRATA = b'garaza/vrata'
T_USER = b'garaza/vrata/user'
T_INIT = b'garaza/validacija/start'


# ------------------
# ---- FUNKCIJE ----
# ------------------

# --- RFID CITAC ----
def rfid_callback():
    reader.init()
    # posalji zahtjev za citanje
    (stat, tag_type) = reader.request(reader.REQIDL)
    if stat == reader.OK:
        # procitaj karticu i dobij uid
        (stat, uid) = reader.SelectTagSN()
        # je li ispravno procitana?
        if stat == reader.OK:
            # broj prislonjene kartice
            card = int.from_bytes(bytes(uid), "little", False)
            if str(card) != DOZVOLJENA_KARTICA:
                # nedozvoljen pokusaj ulaza
                start_alarm()
            else:
                # ispravna kartica, kratki zvuk
                kratki_bip()
                print("Pisem da se vrata otvore i koji korisnik")
                # javi unutrasnjem modulu da otvori vrata
                # javi koji je korisnik za mobilnu aplikaciju
                client.publish(T_VRATA, b'open', retain=False)
                client.publish(T_USER, b'4159772003', retain=False)

# ---- Wifi konekcija ----
def connect_wifi():
    # inicijaliacija
    wlan = network.WLAN(network.STA_IF)
    wlan.active(True)
    if not wlan.isconnected():
        # spoji ako nije vec spojen
        print("Spajam na WiFi...")
        wlan.connect(SSID, PASSWORD)
        while not wlan.isconnected():
            time.sleep(0.2)
    print("WiFi konfiguracija:", wlan.ifconfig())

# ---- MQTT Callback ----
def on_mqtt(topic, msg):
    # prima poruke za gasenje alarma i pocetak validacije 
    global alarm_active, started
    print("MQTT primljeno:", topic, msg)
    if topic == T_ALARM and msg.strip() == b'alarm_off':
        if alarm_active:
            print("Gasi alarm")
            stop_alarm()
        else:
            print("Alarm nije aktivan, ništa za gasiti")
    
    elif topic == T_INIT and msg.strip()==b'start':
        # zapocni validaciju unosa
        timer_keypad.init(period=SCAN_INTERVAL, mode=Timer.PERIODIC, callback=scan_keypad)
        timer_display.init(period=MUX_INTERVAL, mode=Timer.PERIODIC, callback=display_callback)
        started = True

# ---- Setup za MQTT ----
def mqtt_setup():
    connect_wifi()
    client.set_callback(on_mqtt)
    print("Callback postavljen za mqtt")

    while True:
        try:
            print("Pokušaj spajanja klijenta...")
            client.connect()
            print("Klijent uspješno spojen")
            client.subscribe(T_ALARM)
            print("Pretplaćen na topic", T_ALARM)
            client.subscribe(T_INIT)
            print("Pretplaćen na topic", T_INIT)
            break  # izlaz iz petlje ako je uspješno
        except Exception as e:
            print("MQTT greška pri spajanju:", e)
            time.sleep(2)  # pričekaj malo prije novog pokušaja


# --- ALARM KONTROLA ---
def start_alarm():
    global alarm_active
    if alarm_active:
        print("Alarm je već aktivan")
        return
    alarm_active = True
    print("Alarm startovan")
    piezo.high()
    # ukljucen alarm, onemogucen unos
    timer_keypad.deinit()
    timer_display.deinit()
    client.publish(T_ALARM_ACTIVE, b'aktivan', retain=False)

def stop_alarm():
    global alarm_active
    alarm_active = False
    piezo.low()
    print("Alarm ugašen")
    # zaustavi alarm i ponovo omoguci unos
    timer_keypad.init(period=SCAN_INTERVAL, mode=Timer.PERIODIC, callback=scan_keypad)
    timer_display.init(period=MUX_INTERVAL, mode=Timer.PERIODIC, callback=display_callback)

# --- Displej ISR ---
def display_callback(timer):
    # postavlja vrijednost trenutne cifre po redu
    global current_digit, input_pin
    for d in digit_pins: d.value(1)
    for s in seg_pins:   s.value(1)
    dp_pin.value(1)
    s = input_pin + " "*(4 - len(input_pin))
    ch = s[current_digit]
    if ch == ' ':
        seg = BLANK
    elif ch == '-':
        seg = MINUS
    else:
        try:
            # dobij vrijednost segmenata
            seg = DISPLEJ_MAPA.get(int(ch), BLANK)
        except:
            seg = BLANK
    # postavi vrijednosti segmenata
    for i,v in enumerate(seg):
        seg_pins[i].value(v)
    # ukljuci cifru i racunaj koja je iduca po redu
    digit_pins[current_digit].value(0)
    current_digit = (current_digit + 1) & 3

# --- SKENIRANJE TASTATURE ---

# jedan two-way prolaz
def single_scan():
    cand = (None, None)
    # postavi jedan po jedan red na high
    # provjeri ima li kolona da je high
    for ri, rp in enumerate(row_pins):
        rp.high()
        time.sleep_us(3)
        cols = [cp.value() for cp in col_pins]
        rp.low()
        act = [i for i,v in enumerate(cols) if v]
        if len(act)==1:
            cand = (ri, act[0])
            break
        # detektovan je ghosting, prekini
        if len(act)>1:
            return (None,None,None)
    if cand[0] is None:
        return (None,None,None)
    ri,ci = cand
    # rekonfiguracija pinova
    for rp in row_pins: rp.init(Pin.IN, Pin.PULL_DOWN)
    for cp in col_pins: cp.init(Pin.OUT)
    # drugi prolaz, sada sa novom konfiguracijom
    for i,cp in enumerate(col_pins):
        cp.value(1 if i==ci else 0)
    time.sleep_us(3)
    rows_back = [rp.value() for rp in row_pins]
    # vrati izvornu konfiguraciju
    for rp in row_pins: rp.init(Pin.OUT); rp.low()
    for cp in col_pins: cp.init(Pin.IN, Pin.PULL_DOWN)
    # tipka detektovana ispravno
    if rows_back.count(1)==1 and rows_back[ri]==1:
        return (ri,ci, matrix_keys[ri][ci])
    return (None,None,None)

# ISR za skeniranje tastature
def scan_keypad(timer):
    # potrebno 4 puta uzastopno detektovati istu tipku da se prihvati
    global _last_rc, _streak, _debounced_rc
    # jedan two-way prolaz
    r,c,key = single_scan()
    raw = (r,c)
    if raw==_last_rc:
        _streak += 1 # povecaj streak
    else:
        _last_rc, _streak = raw,1 # streak je na 1
    
    # Ako je postignut trazeni streak od 4
    if _streak>=DEBOUNCE_STREAK:
        if _debounced_rc==(None,None) and raw!=(None,None):
            _debounced_rc = raw
            # Regulisi parsiranje pina
            handle_key(key)
        elif _debounced_rc!=(None,None) and raw==(None,None):
            _debounced_rc = (None,None)

# Blinkanje znaka - na pogresnom unosu
def blink_minus(duration=2, interval=0.3):
    timer_display.deinit()
    end_time = time.time() + duration
    while time.time() < end_time:
        for d in digit_pins: d.value(1)
        for s in seg_pins:   s.value(1)
        dp_pin.value(1)
        time.sleep(interval)
        # sve cifre na -
        for d in digit_pins:
            for i, v in enumerate(MINUS):
                seg_pins[i].value(v)
            d.value(0)
        time.sleep(interval)
        for d in digit_pins: d.value(1)
    # ponovo omoguci prikaz displeja
    timer_display.init(period=MUX_INTERVAL, mode=Timer.PERIODIC, callback=display_callback)

def clear_display():
    # gasi sve segmente
    for digit in digit_pins:
        digit.value(1)

    for seg in seg_pins:
        seg.value(1)  

    dp_pin.value(1)

# Blinkanje znaka . na ispravnom unosu
def flash_decimal_points(duration=2):
    timer_display.deinit()
    t_end = time.ticks_add(time.ticks_ms(), duration * 1000)

    while time.ticks_diff(t_end, time.ticks_ms()) > 0:
        # Uključi samo DP na svim ciframa
        for i in range(4):
            clear_display()  
            digit_pins[i].value(0)  
            dp_pin.value(0)  
            time.sleep(0.005)
            dp_pin.value(1) 
            digit_pins[i].value(1)  
        time.sleep(0.2)  
    timer_display.init(period=MUX_INTERVAL, mode=Timer.PERIODIC, callback=display_callback)

# Parsiranje PIN-a
def handle_key(key):
    global input_pin, wrong_attempts
    if key=='#':
        # pokusaj potvrde unosa
        # vidi je li duzina pina ispravna i je li ispravan pin
        if len(input_pin) == 4:
            if input_pin == ISPRAVAN_PIN:
                print("Ispravan PIN, alarm ne aktivira se")
                wrong_attempts = 0
                # Prikazi ispravno stanje
                flash_decimal_points()
                kratki_bip()
                print("Pisem da se vrata otvore i user")
                # javi unutrasnjem modulu da otvori vrata
                # javi koji je user zbog mobilne aplikacije
                client.publish(T_VRATA, b'open', retain=False)
                client.publish(T_USER, b'8273', retain=False)
            else:
                # neispravan pokusaj, prikazi stanje
                wrong_attempts += 1
                blink_minus()
                print("Pogrešan PIN, ", wrong_attempts)
                # na trecem uzastopnom se pali alarm
                if wrong_attempts == 3: 
                    wrong_attempts = 0
                    start_alarm()
            input_pin = ""
        else:
            input_pin = ""
    elif key=='*':
        input_pin = ""
    elif key.isdigit() and len(input_pin)<4:
        input_pin += key

# Kratka zvucna potvrda ispravnog unosa
def kratki_bip():
    piezo.high()
    time.sleep(0.5)
    piezo.low()

# ------------------------
# ---- POCETNO STANJE ----
# ------------------------
mqtt_setup()
last_rfid_check = time.ticks_ms()

# Glavna petlja
while True:
    # desava se da klijent gubi konekciju s temom
    # ovo je odrzava zivom
    client.subscribe(T_ALARM)
    # ako nije zapoceta validacija provjeravaj i tu temu
    if not started:
        client.subscribe(T_INIT)
    # provjeri poruku
    client.check_msg()
    # skeniraj RFID
    # ako je zapocela validacija
    # ako alarm nije aktivan
    # i ako je prosla 1.5 s
    if started and not alarm_active and time.ticks_diff(time.ticks_ms(), last_rfid_check) > RFID_INTERVAL:
        rfid_callback()
        last_rfid_check = time.ticks_ms()
    time.sleep(0.05)

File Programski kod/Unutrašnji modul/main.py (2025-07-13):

from machine import Pin, PWM, Timer
import machine
import time
import network
from simple import MQTTClient

# ----------------------------
# ---- VARIJABLE I PINOVI ----
# ----------------------------
door_open = False # varijabla stanja
# Servo setup
servo_pin = Pin(16)
servo = PWM(servo_pin)
servo.freq(50)
# Senzor vani setup
TRIGGER_PIN = 3
ECHO_PIN = 2
BRZINA_ZVUKA = 0.0343 # u cm po mikrosekundi
trigger = Pin(TRIGGER_PIN, Pin.OUT)
echo = Pin(ECHO_PIN, Pin.IN)
signal_on = 0
distanca = 0
# Touch senzor
touch_pin = Pin(5, Pin.IN)

# ----------------
# ---- TIMERI ----
# ----------------
timer_senzor = Timer()
timer_close_safe = Timer()
# periodi u ms
TIMER_CLOSE_MS = 120000
TIMER_SENZOR_MS = 1000

# ---------------------
# ---- WIFI I MQTT ----
# ---------------------
# Wifi podaci
ssid = 'ETF-WiFi-Guest'
password = ''
# MQTT konekcija
client_id = 'pico-client-dalila196657'
broker = 'broker.hivemq.com'
client = MQTTClient(client_id, broker)
# MQTT teme
T_INIT = b'garaza/validacija/start'
T_VRATA = b'garaza/vrata'


# ------------------
# ---- FUNKCIJE ----
# ------------------

# Wi-Fi konekcija
def connect_wifi():
    # inicijalizacija 
    wlan = network.WLAN(network.STA_IF)
    wlan.active(True)

    if wlan.isconnected():
        print('Već povezan na mrežu:', wlan.ifconfig())
    else:
        # povezi se ako nije vec povezan
        print('Povezujem se na mrežu...')
        wlan.connect(ssid, password)
        while not wlan.isconnected():
            time.sleep(1)
        print('Povezan na mrežu:', wlan.ifconfig())

# Mjeri distancu od objekta
# ISR za timer
def mjeri(timer):
     global signal_on, trigger, echo
     # salje se kratki puls na trigger
     trigger.off(); time.sleep_us(2)
     trigger.on(); time.sleep_us(10)
     trigger.off()
     
     try:
          # slusanje na echo
          # signal_on = vrijeme u mikrosekundama
          # vrijeme za koje je echo pin imao vrijednost high
          signal_on = machine.time_pulse_us(echo, 1, 10000000)
     except OSError:
          print("Timeout dok echo nije na HIGH - nema objekta")
          return

    # sa brzinom zvuka dobije se distanca u cm
    # dijeli se sa 2 jer nam treba distanca u jednom smjeru samo
     distanca = (signal_on * BRZINA_ZVUKA)/2
     print("Distanca od objekta je ", distanca, "cm")
     if distanca < 7:
        # automobil se priblizio dovoljno
        # validacija unosa moze da pocne
        # javljamo vanjskom modulu putem MQTT
        timer_senzor.deinit() # vise ne treba senzor udaljenosti
        client.publish(T_INIT, b'start', retain = False)

# Funkcija za mapiranje ugla u PWM duty
def mapiranje_intervala(x, ulazni_min, ulazni_max, izlazni_min, izlazni_max):
    return (x - ulazni_min) * (izlazni_max - izlazni_min)/(ulazni_max - ulazni_min) + izlazni_min

# Kontrola servo motora
def pisi_servo(pin, ugao):
    puls = mapiranje_intervala(ugao, 0, 180, 0.5, 2.5)  # ms
    duty = int(mapiranje_intervala(puls, 0, 20, 0, 65535))  # konvertuje u 16-bitni duty
    pin.duty_u16(duty)

# Funkcije za otvaranje i zatvaranje vrata
def open_door():
    global door_open
    print("Otvaram vrata...")
    door_open = True # postavi varijablu stanja
    pisi_servo(servo, 180)  # potpuno otvoreno
    # inicijaliziraj timer
    # ako vrata nisu zatvorena nakon 2 min, zatvara ih njegov ISR
    timer_close_safe.init(period = TIMER_CLOSE_MS, mode=Timer.ONE_SHOT, callback = safe_close)

def close_door():
    global door_open
    print("Zatvaram vrata...")
    door_open = False
    pisi_servo(servo, 80)  # zatvoreno, nije 90 zbog koristenog servo motora, ovo je bolje odgovaralo
    # dosli smo u stanje gdje bi ponovo mogla trebati validacija unosa
    # aktiviramo senzor udaljenosti za tu svrhu
    timer_senzor.init(period = TIMER_SENZOR_MS, mode = Timer.PERIODIC, callback = mjeri)

# Setup MQTT klijenta
def mqtt_setup():
    # spoji se na wifi i pretplati se na temu s koje slusas poruke
    connect_wifi()
    client.set_callback(sub_cb)
    client.connect()
    client.subscribe(T_VRATA)
    print("Spreman za primanje MQTT poruka...")

# MQTT callback
def sub_cb(topic, msg):
    # MQTT klijent prima poruke sa teme garaza/vrata
    # sluzi za kontrolu vrata
    print("Poruka primljena:", topic.decode(), msg.decode())
    if msg.decode() == "open":
        open_door()
        print("Otvaram vrata")
    elif msg.decode() == "close":
        close_door()
        print("Zatvaram vrata")

# ISR za touch senzor
def touch_senzor(pin):
    # radi suprotnu akciju od trenutnog stanja garaznih vrata
    if door_open:
        close_door()
        print("Zatvaram vrata")
    else:
        open_door()
        print("Otvaram vrata")
    
# ISR za timer automatskog zatvaranja
# Ako su vrata ostala otvorena nakon 2 min zatvaraju se automatski
def safe_close(timer):
    if door_open:
        close_door()

# ------------------------
# ---- POCETNO STANJE ----
# ------------------------
mqtt_setup()
close_door()
print("Zatvaram vrata")
timer_senzor.init(period = TIMER_SENZOR_MS, mode = Timer.PERIODIC, callback = mjeri)
touch_pin.irq(handler = touch_senzor, trigger = Pin.IRQ_RISING)

# Glavna petlja
# provjeravanje MQTT poruke
while True:
    client.check_msg()
    time.sleep(0.05)
